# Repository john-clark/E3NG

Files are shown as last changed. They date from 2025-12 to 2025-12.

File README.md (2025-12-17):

# E3NG Repo

This was mirrored from the RH3D website repo because I wanted to have one place to keep track of everything. I have pulled out a lot of the website stuff in order to have just the information I am interested in. This repo uses LFS so if you use the github download zip it will not include the large files.

### This is not meant as an official repo or as anything but my personal E3NG repo

All credits go to the [RH3D E3NG](https://rh3d.xyz/).

If you stumbled upon this that is where you should go for more information.

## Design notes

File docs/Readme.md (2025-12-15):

# Documentation

### Original

While the pdf's that the project puts out are very well put together they lack key information and are not well suited to the build process or the revision process. The author makes changes without producing a change log, sometimes changing key information. It s sort of funny that these files will not open with Adobe, I had to open them with Firefox and then print them to a PDF to open them with Adobe so I could compare the changes. This is not a fun way to do this but I think the project needs to do a better job with the versioning and documentation, some of the information removed is key to the project and there is quite a bit of missing or incorrect information.

### Extracted

!WIP I extracted the LONG pdf files and put them into o and s folders. o is for the old doc and s is the current. I didn't have time to finish going through them, but the o folder has some pages that were removed from the current docs. I hope to eventually finish digging through them and combining them with the web site doc and finally they should be matched up with the models so you can quickly look at the parts that are being explained. !TODO WIP

NOTEs: The printable frame information was removed, and it looks like they settled on the so called ultimate frame. I think this is because the E3NG project has a major flaw with all the corners being printed and therefore subject to no good alignment. The maintainers new project seems to correct this and gets rid of most of the 3d printed parts used in squaring the frame. However with a 3d printed gantry this point is moot since that will also have issues. The revised gantry has several problems compared to the old gantry such as easy of disassembly.

Also if you are going to be printing the bottom skirts you might as well ignore pages 19-20 and 23.

The  Electronics section was so bad I didn't bother to compare.

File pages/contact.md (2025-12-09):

---
title: Contact ✉️
layout: default
nav_order: 110
description: "Reach out to RH3D with questions, feedback, or collaboration ideas. Connect with the maker behind Ender 3 NG, Virtu E3, and other 3D printer upgrade projects."
permalink: /contact
---

<div class="responsive-iframe-container">
  <iframe
          src="https://docs.google.com/forms/d/e/1FAIpQLSdQgB7Aw7cdLq2ng6Stj-KTayaxvqaDmWC6Ourq5sMZkLAirw/viewform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"
          width="100%"
          height="1080px"
          frameborder="0"
          marginheight="0"
          marginwidth="0">
    Loading…
  </iframe>
</div>

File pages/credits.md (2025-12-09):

---
title: Credits
layout: default
nav_order: 60
description: "Discover the makers, contributors, and open-source projects behind E3NG. RH3D thanks the DIY 3D printing community for sharing innovation and inspiration."
permalink: /credits
---
# THANK YOU
{: .text-center }

- Everyone who decides to give support / donates to the project.
- All our Discord members for creating an awesome place to chat and for helping each other.
- Everyone who decides building the printer and contributes to the world of E3NG.
- Bigtreetech
- Creality3D
- [Discovery Sky]

---
Projects used (remixed) in the E3NG.
- [WobbleX] by MirageC
- [Klicky probe] by jlas
- [KlickyPCB dock] by SP1986
- [M4 Extruder] by VoronDesign
- [Sherpa mini] and [Sherpa micro] by Annex Engineering
- [HextrudORT] by MirageC
- [Vz-HextrudORT] by Vez3D
- [ProtoXtruder], [ProtoXtruder 2.0] and [Hummingbird extruder] by nhchiu
- [Klipper]
- [Marlin]

And others.
- [Rolohaun3D] for the inspiration of using linear rods as a structural part of the frame.
- [MirageC], [Vez3D], [eddietheengineer], [VoronDesign], [Prusa3D] and many others for their dedication to research in 3D printing.

[Discovery Sky]: https://github.com/markniu
[WobbleX]: https://github.com/MirageC79/Interfaces-for-WobbleX-integration
[Klicky probe]: https://github.com/jlas1/Klicky-Probe
[KlickyPCB dock]: https://www.teamfdm.com/files/file/729-pcb_klicky_mount/
[M4 Extruder]: https://github.com/VoronDesign/Mobius-Extruder
[Sherpa mini]: https://github.com/Annex-Engineering/Sherpa_Mini-Extruder/
[Sherpa micro]: https://github.com/Annex-Engineering/Sherpa_Micro-Extruder
[HextrudORT]: https://github.com/MirageC79/HextrudORT
[Vz-HextrudORT]: https://github.com/VzBoT3D/Vz-HextrudORT
[ProtoXtruder]: https://www.printables.com/cs/model/436425-protoxtruder
[ProtoXtruder 2.0]: https://www.printables.com/cs/model/822947-protoxtruder-20
[Hummingbird extruder]: https://www.printables.com/cs/model/367706-hummingbird-extruder
[Klipper]: https://www.klipper3d.org/
[Marlin]: https://marlinfw.org/
[Rolohaun3D]: https://github.com/rolohaun/Rook-180

[MirageC]: https://www.youtube.com/@MirageC
[Vez3D]: https://www.youtube.com/@Vez3D
[eddietheengineer]: https://www.youtube.com/@eddietheengineer
[VoronDesign]: https://github.com/VoronDesign
[Prusa3D]: https://github.com/prusa3d

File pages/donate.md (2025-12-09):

---
title: Support the development ❤️
layout: default
nav_order: 99
description: "Support RH3D's open-source development of Ender 3 NG, Virtu E3, and DIY 3D printing projects. Your donation helps keep innovation alive and accessible."
permalink: /donate
---
# SUPPORT THE DEVELOPMENT
{: .text-center }

Ender 3 NG will always be free to use, but developing a project of this size, variability and compatibility is a huge amount of work. It takes lot of time, effort and requires resources to test and improve the design and maintain it up to date.

With your donation, you are helping to keep the project alive, maintained and growing as well as opening the possibility for other future projects. You can use some of the links below.

You can also use affiliate links in the BOM which also helps with no added cost to you.

#### Thank you a lot!
{: .text-center }

<div>
<script type='text/javascript' src='https://storage.ko-fi.com/cdn/widget/Widget_2.js'></script><script type='text/javascript'>kofiwidget2.init('Ko-fi', '#28b5e0', 'E1E1JZ5FS');kofiwidget2.draw();</script> 
</div>
{: .text-center .mt-8 }

<div id="donate-button-container">

<script src="https://www.paypalobjects.com/donate/sdk/donate-sdk.js" charset="UTF-8"></script>
<script>
PayPal.Donation.Button({
env:'production',
hosted_button_id:'LR94TRQXMGW46',
image: {
src:'../assets/images/paypal_donate.png',
alt:'Donate with PayPal button',
title:'PayPal - The safer, easier way to pay online!',
}
}).render('#donate-button');
</script>
</div>
{: .text-center .mt-5 }

Patreon (https://www.patreon.com/RH3D_cz)
{: .text-center }

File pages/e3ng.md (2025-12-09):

---
title: E3NG v1.2
layout: default
has_children: true
nav_order: 20
description: "Transform your Ender 3 into a powerful CoreXY machine with E3NG by RH3D. Reuse up to 78% of original parts for a faster, more precise 3D printing experience."
permalink: /e3ng
---
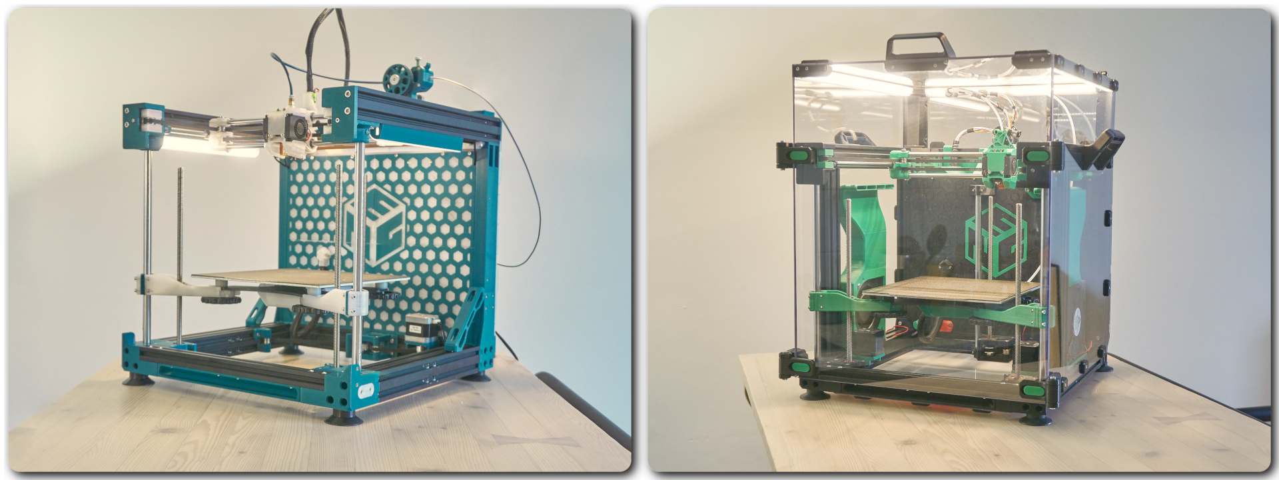
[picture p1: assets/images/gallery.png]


# E3NG (ENDER 3 NG)
{: .text-center }

**Take your old, unused Creality Ender 3 and turn it into something amazing—something fast, powerful, precise, and reliable and enjoy the new level of tinkering.**
{: .text-center .mb-6 }

E3NG is a DIY project focused on reviving up to **78%*** of parts from your original printer and giving them a brand-new purpose. Many of us started with the simple Ender 3, and it taught us a lot—but 3D printing has evolved, and it’s time to step up. That’s exactly what this conversion is all about.

Originally designed for the Ender 3 Pro, it also supports other models like the V2, Neo, and even the non-Pro variant. The goal? Reuse as much as possible and build a machine that’s significantly faster, more reliable, easy to enclose, and still totally upgradable—because let’s face it, not everyone with an Ender 3 is done tinkering.

Whether you go with a low-budget build or max out performance, you’ll turn your Ender 3 into a CoreXY machine that honors its roots—while bringing it into the **Next Generation** of printers.

There are two versions to choose from:
 - **v1.2S (standard)** offers a more streamlined, kit-style approach with clear instructions and a straightforward build path—perfect if you prefer to keep things more simple.
 - **v1.2 (advanced)** is for those who like to go deep into the project, tweak every detail, giving you the flexibility to configure your printer to match your own preferences and setup.

[E3NG v1.2S (standard)]{: .btn .fs-6 .fw-300 .text-yellow-300 .v-align-middle .mr-3 .mb-8 .mt-6 } [E3NG v1.2 (advanced)]{: .btn .fs-6 .fw-300 .text-yellow-300 .v-align-middle .ml-3 .mb-8 .mt-6 }
{: .text-center }

# "NG = NEXT GENERATION"
{: .text-center }

#### PRINTER FEATURES
- Build volume _(X-Y-Z)_: 235 x 235 x 245 mm (max Z depends on the hotend used)
- Printer size _(X-Y-Z)_: 407 x 438 x 440 mm ( 455 x 485 x 548 mm enclosed )
- CoreXY motion system
- Linear rods for X, Y and Z axis.
- Stable Z axis with 3 leadscrews and 3 linear rods.
- Enclosed electronics on the back of the printer.
- DIN rails in electronics compartment for easy organization.
- Anti Z wobble system within the bed carriage.
- Easy to enclose.

#### BONUS FEATURES
- Reuses up to **78%*** of the original parts.
- Fanducts optimised with CFD analysis tools.
- Toolhead compatibility with majority of hotends, extruders and bed probes.
- Toolhead with 4 variants of part cooling - dual 4010, dual 4020, dual 5015, CPAP.
- Files designed for easy printability and functionality.

#### OPTIONAL FEATURES (in the v1.2 - advanced)
- Under bed fan for air circulation and faster chamber heating.
- Active cooling for AB stepper motors.
- Auxiliary fans with 12032 blowers.
- Lasercut metal bed carriage for the best stability.
- Single or triple Z stepper motors.
- and more - see the [CONFIGURATION] options

continue to:
{: .text-right .lh-0 .pt-8 }

[INTO THE PROJECT]{: .btn .fw-300 .fs-6 .text-yellow-300 }
{: .text-right }

---
***up to 78%** = Measured by weight of the parts from stock Ender 3 Pro. The percentage is calculated when reusing the majority of parts incl. motherboard, screen, screws, hotend (which is all possible). When using the required minimum of parts, **68%** is reused.*

*For extra **9%** of part reusage, there are side projects specifically designed to reuse more of the leftover parts - heat set insert press, camera slider (will be released to public later). The number of projects might grow in the future.*

[E3NG v1.2S (standard)]: https://rh3d.xyz/E3NG_v1_2/standard
[E3NG v1.2 (advanced)]: https://rh3d.xyz/E3NG_v1_2/advanced
[INTO THE PROJECT]: https://rh3d.xyz/into.html
[CONFIGURATION]: https://rh3d.xyz/E3NG_v1_2/advanced/config

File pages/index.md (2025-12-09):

---
title: RH3D
layout: home
nav_order: 10
description: "Explore RH3D's custom Ender 3 upgrades and DIY 3D printing projects. Give your printer a second life and join a passionate maker community."
permalink: /
---
# E3NG (ENDER 3 NG)

The legacy design that transforms your basic Ender 3 into a Next Generation machine. Want to keep it simple and affordable or go fully loaded? The choice is yours.

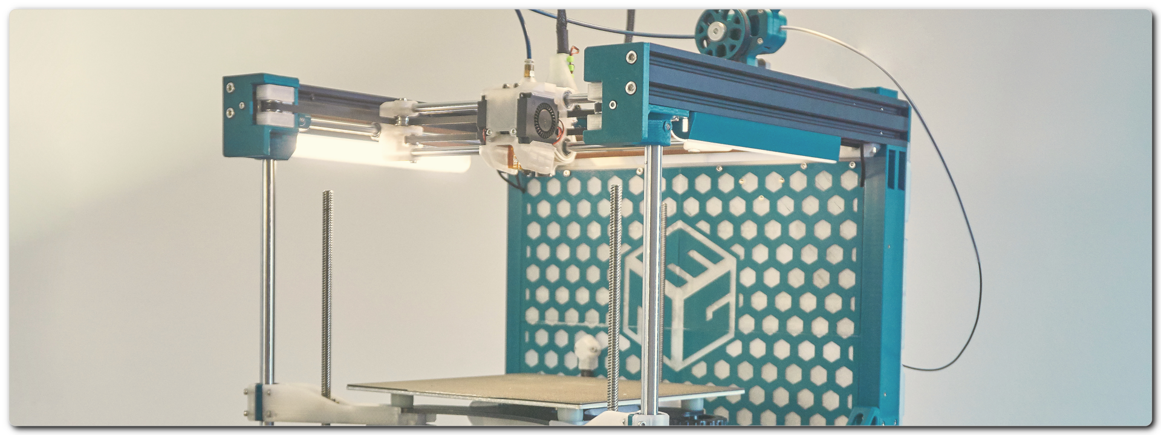
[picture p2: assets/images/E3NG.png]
E3NG (https://rh3d.xyz/e3ng)

{: .text-center }

# VIRTU E3
{: .mt-9 }

The second-generation hero, built to revive all the unused Enders. Purity, speed, precision — this is Virtu.

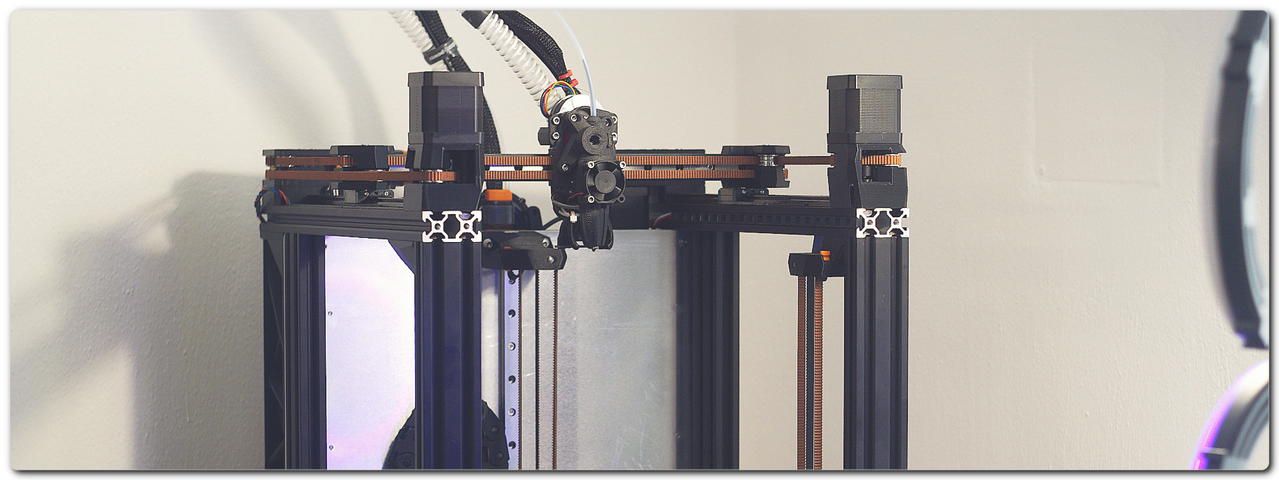
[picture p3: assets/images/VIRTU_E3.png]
VirtuE3 (https://rh3d.xyz/virtu)

{: .text-center }

---
# WELCOME!
{: .text-center }

If you're into 3D printing, love to tinker, and enjoy building things yourself, you’re in the right place.

What began as a hobby and a personal project quickly evolved into a true passion. This site is where you'll find all my major designs, complete with the information you need. Feel free to explore the site, check out the YouTube and Instagram, and join our amazing community on Discord!

[YouTube]{: .btn .fw-400 .text-yellow-300 .v-align-middle .mb-8 } [Instagram]{: .btn .fw-400 .text-yellow-300 .v-align-middle .ml-5 .mr-5 .mb-8 } [Join the Discord]{: .btn .fw-400 .text-yellow-300 .v-align-middle .mb-8 }
{: .text-center }

---
## About RH3D

Hi! I’m Radek—engineer, architect, woodworker, and maker by nature. I was born into a family of engineers in the Czech Republic, and from a young age, I found joy in creating. Whether it was building something with my hands or dreaming up designs on paper, I was always drawn to the process of turning ideas into reality.

My journey has taken me through engineering, woodworking, and ultimately back to my original profession—architecture. But beyond the workshops and design boards, I’m also a proud husband and loving father. My family keeps me grounded and inspired, and they’ve been my biggest supporters through every prototype and late-night tinker session.

## How did I get into 3D printing?

I was always fascinated by the technology, but without a clear use case, I couldn't justify owning a printer. That changed when I got an old Ender 3 Pro to support a few side projects in my woodworking business. Who could’ve guessed I’d get completely hooked—printing, upgrading, modifying... like most of the Ender 3 owners, right?

## The first Ender 3 NG

Once you dive in, it’s tough to stop. I realized there were more capable designs within reach. After plenty of research, modifications, and testing, the Ender 3 NG was born. It started as a personal project to convert an Ender 3 into an enclosed CoreXY machine on a budget—but it grew into something far more meaningful. This journey has led me to create amazing things, build a thriving community, and connect with passionate people from around the world.

[Join the Discord]: https://discord.com/invite/Zkvu6uu2AR
[Instagram]: https://www.instagram.com/RH3D_cz
[YouTube]: https://www.youtube.com/@RH3D_cz?sub_confirmation=1

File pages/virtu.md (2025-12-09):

---
title: VIRTU E3
layout: default
has_children: false
nav_order: 40
description: "Turn your Ender 3 into an unstopable coreXY machine! Speed, precision, purity - that is Virtu E3 by RH3D."
permalink: /virtu
---
# VIRTU E3
{: .text-center }

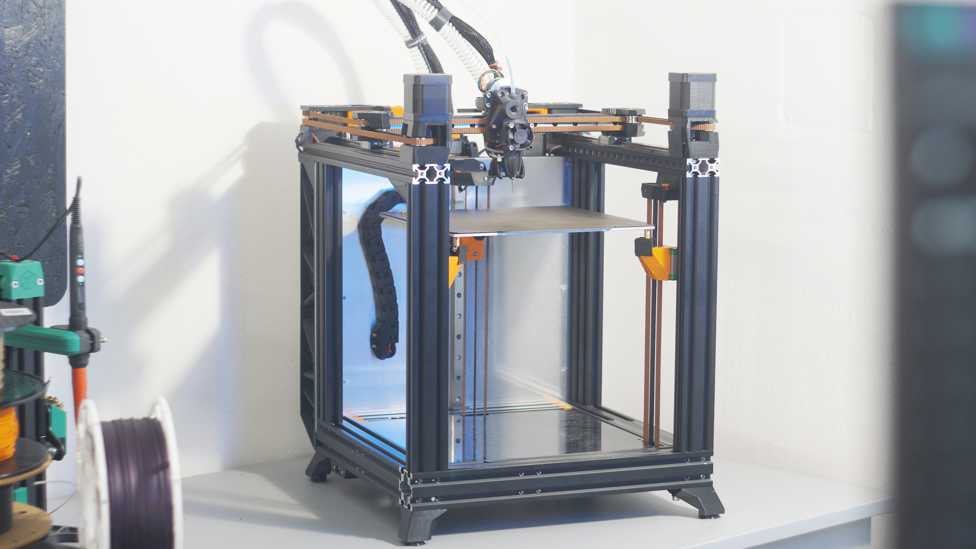
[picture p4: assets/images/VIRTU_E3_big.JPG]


#### CURRENTLY IN DEVELOPMENT AND TESTING
{: .text-center }

---

*Thank you to everyone who helps bringing such projects into reality, especially all my Patreon members and supporters, but also companies like Fabreeko, BigTreeTech, LDO motors, FilamentPM.*

*Thank you all, who are interested into my projects!*

If you also want to help supporting the development, you can do so through any of the [DONATE](https://rh3d.xyz/donate) options. Any kind of support is greately appreciated.
{: .text-center }

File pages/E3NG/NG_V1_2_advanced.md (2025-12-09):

---
title: v1.2 - (advanced)
layout: default
parent: E3NG v1.2
has_children: true
nav_order: 30
description: "Customize your E3NG v1.2 CoreXY printer with modular upgrades, advanced configurations, and full control over sourcing. A flexible DIY platform for expert builders."
permalink: /E3NG_v1_2/advanced
---

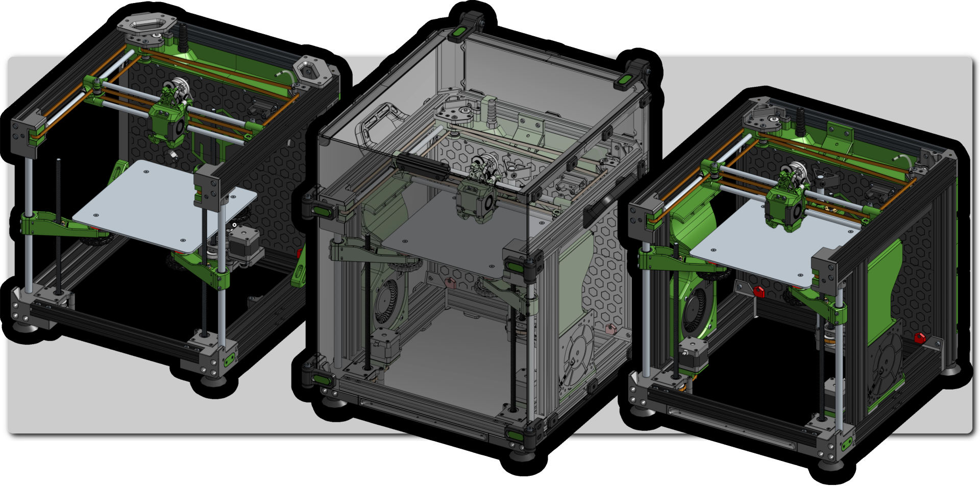
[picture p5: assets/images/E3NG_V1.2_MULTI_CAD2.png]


# E3NG v1.2
{: .text-center }
#### v1.2 = advanced version (customisable)
{: .text-center }

The v1.2 "advanced" is built for more experienced users who value modularity, higher configuration control, and overall flexibility. Unlike the standard version, v1.2 is not bound by kit constraints and instead offers a configurator-driven workflow that helps you setup the printer build based on your own preferences and gives you more customisation options.

Builders may choose to start with a different frame setup or incorporate upgrades such as LEDs, auxiliary cooling, stepper motor cooling, CNC-cut bed carriage, triple-Z motor configuration and others. These options are documented and categorized in the official configuration guide, allowing the end-user to balance cost, complexity, and performance according to their specific goals.

Due to the diversity of possible configurations, sourcing for the v1.2 requires manual part selection. To assist in this process, the configurator generates a tailored Bill of Materials with direct links to vetted sellers and clearly annotated specifications. This ensures that while the build is more demanding, it remains accessible to users with a clear roadmap.

The v1.2 advanced variant is best described as a platform for tinkering, experimentation, personalization, and performance tuning—offering high degree of flexibility in the E3NG family.

continue to:
{: .text-right .lh-0 .pt-8 }

[CONFIGURATION]{: .btn .fs-6 .fw-300 .text-yellow-300 }
{: .text-right }

[CONFIGURATION]: https://rh3d.xyz/

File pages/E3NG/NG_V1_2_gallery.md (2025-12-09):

---
title: Gallery
layout: default
parent: E3NG v1.2
#has_children: true
nav_order: 1
description: "Browse E3NG v1.2 build photos and wallpapers. See real CoreXY conversions of Ender 3 printers powered by RH3D’s open-source designs and community creativity."
permalink: /E3NG_v1_2/gallery
---
# WALLPAPERS
{: .text-center }

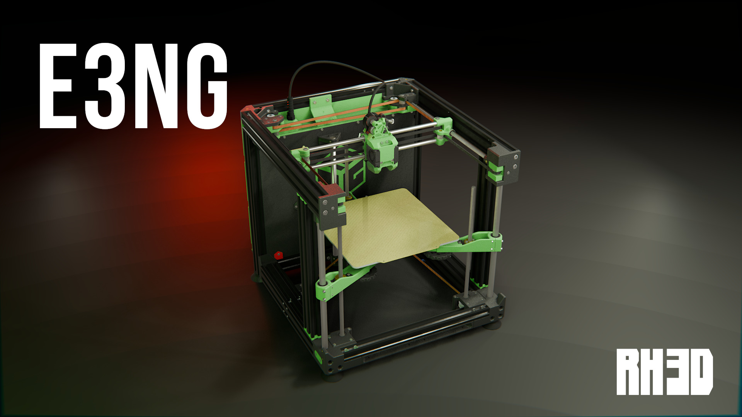
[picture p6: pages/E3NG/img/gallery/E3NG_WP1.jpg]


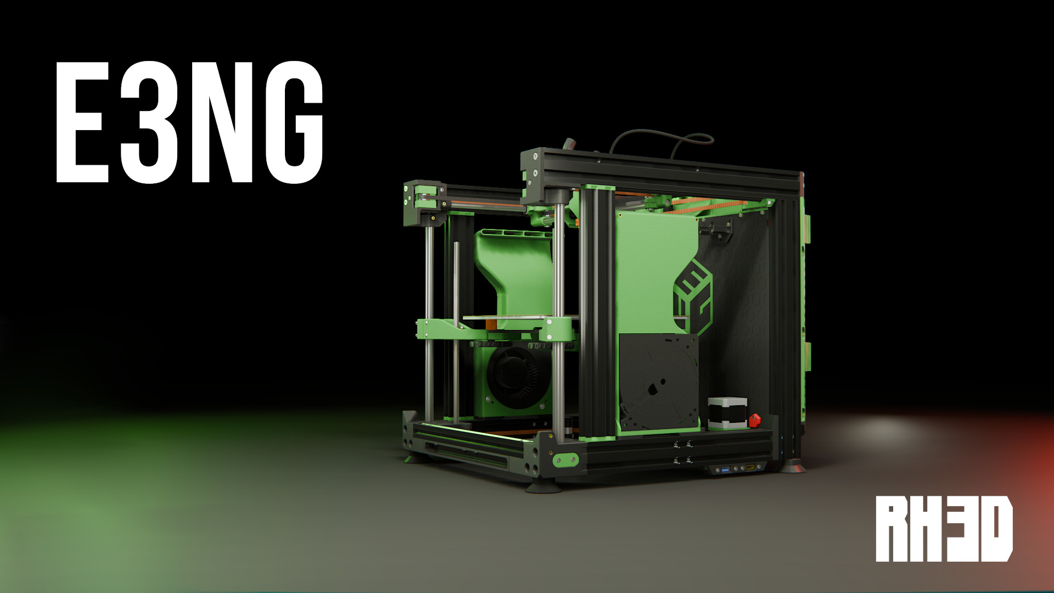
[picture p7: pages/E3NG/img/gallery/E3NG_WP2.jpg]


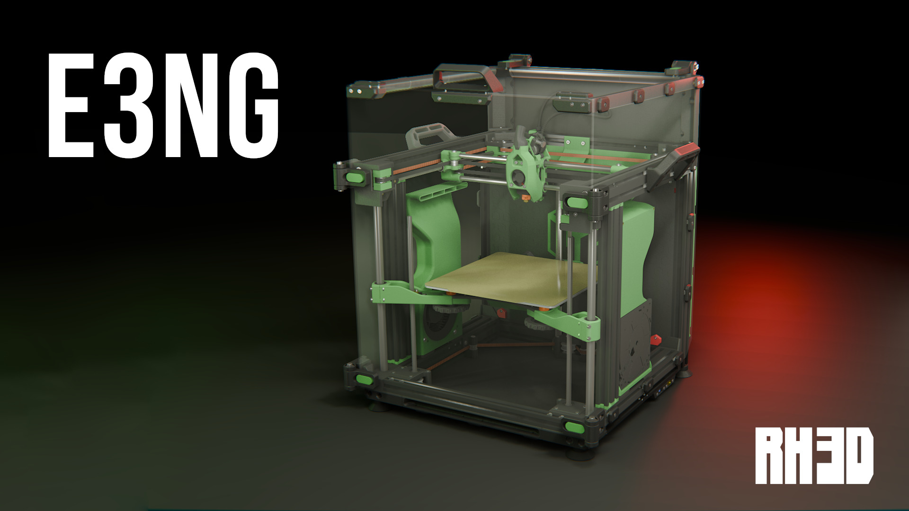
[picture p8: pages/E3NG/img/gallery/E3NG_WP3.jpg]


# PHOTOS
{: .text-center }

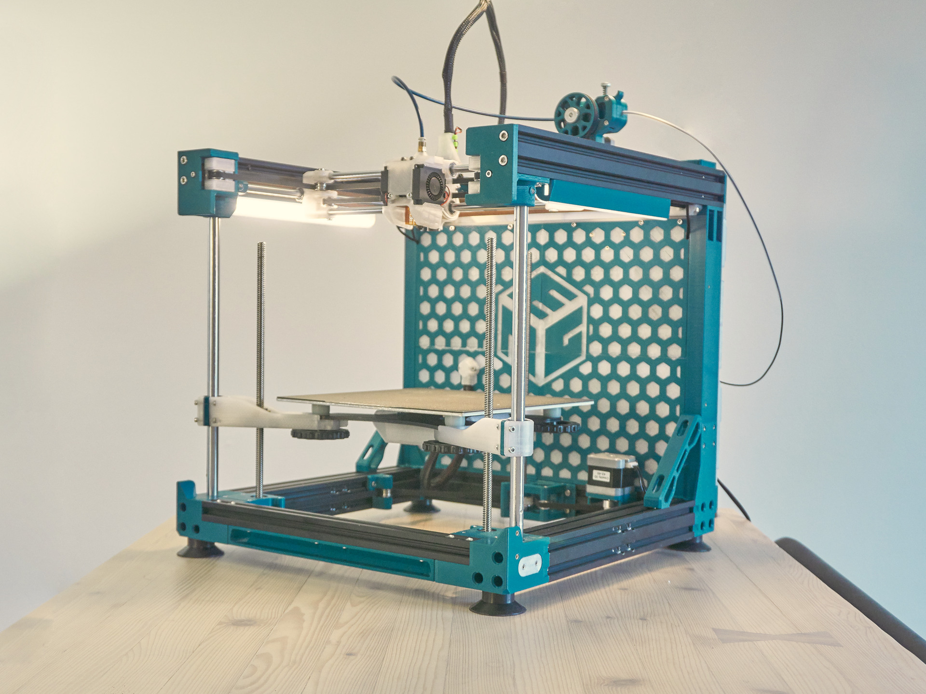
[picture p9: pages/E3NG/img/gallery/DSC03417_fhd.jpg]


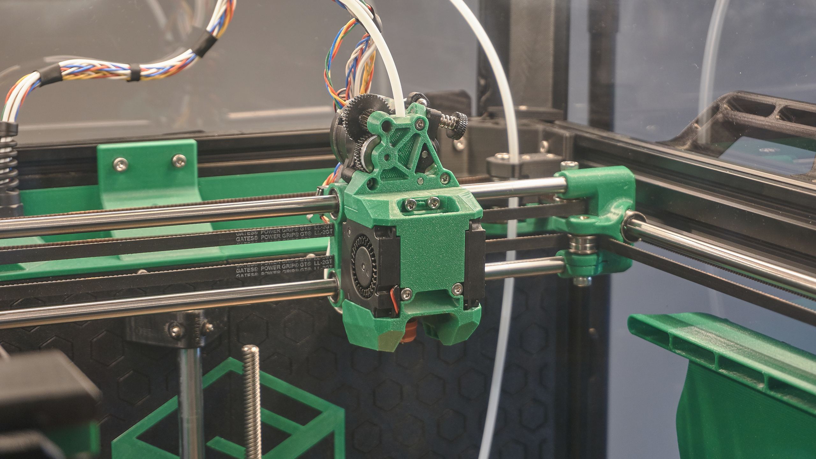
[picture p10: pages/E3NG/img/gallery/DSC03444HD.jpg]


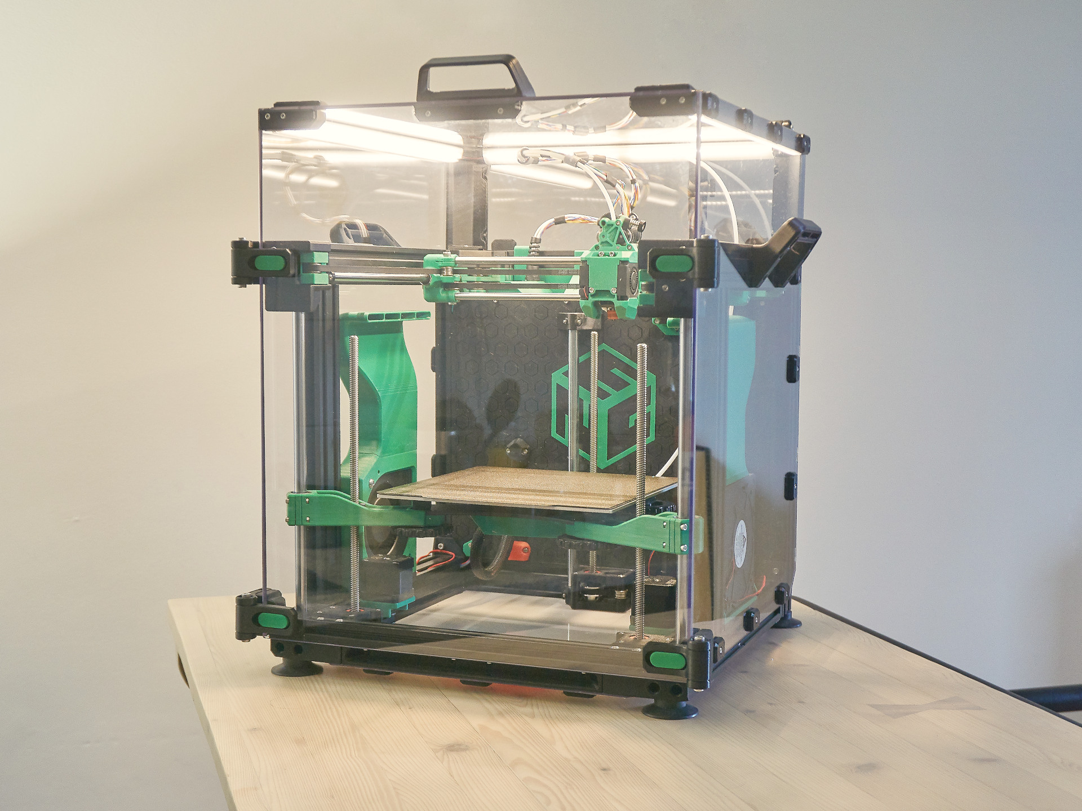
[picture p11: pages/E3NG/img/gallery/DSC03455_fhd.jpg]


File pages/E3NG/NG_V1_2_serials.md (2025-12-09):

---
title: Serial numbers
layout: default
parent: Final steps
#has_children: true
nav_order: 30
description: "Apply for an official serial number for your E3NG v1.2 build. Showcase a finished CoreXY printer and join the lineup of verified RH3D makers."
permalink: /E3NG_v1_2/final_setup/serial_number
---
# SERIAL NUMBERS
{: .text-center }

Just like many of the other known DIY printers, you can get serial number even for your own Ender 3 NG.
The main list of serial numbers and announcements are hosted on Discord server but it is not required to join the Discord server.

All you have to do is meet the requirements and apply for the serial in the link below.

#### Requirements to obtain a serial number.
- Majority of the printer must be based on the Ender 3 NG project. Some smaller mods are allowed but the main goal of serial numbers is to participate in the official project path so highly modified printer may not be approved. The main frame and the X, Y and Z motion systems have to be stock or with minor changes, although you can use different toolhead.
- The printer must be fully functional and tuned to print well without major noticable issues or print quality issues.
- The printer must be finished and not look half done even though it is printing fine. No hanging wires and uncovered electronics are allowed.
- You must upload a video of the printer running where it is well visible and also show that it is actualy printing. Print something at least few centimeters in size.

{: .note }
Remember, it is not a race to get your serial number as soon as possible but rather an oportunity to present your new and pretty printer and add to the line of other nicely build printers.

# SERIAL NUMBER REQUEST
{: .text-center }

To request the serial number, fill the form on the link below:
{: .text-center .lh-0 }

[REQUEST A SERIAL]{: .btn .fs-6 .fw-300 .text-yellow-300 }
{: .text-center }

After your serial number request is succesfully processed, it will be announced on discord channel with provided information and you will be notified, if you are not a member of our Discord server, don't forget to include your e-mail address.

[REQUEST A SERIAL]: https://forms.gle/4JTC2YdJKMqADTAX6

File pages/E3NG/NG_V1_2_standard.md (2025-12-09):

---
title: v1.2S - (standard)
layout: default
parent: E3NG v1.2
has_children: true
nav_order: 20
description: "E3NG v1.2S offers a guided CoreXY upgrade for your Ender 3. Build faster with curated kits, simplified instructions, and streamlined compatibility."
permalink: /E3NG_v1_2/standard
---
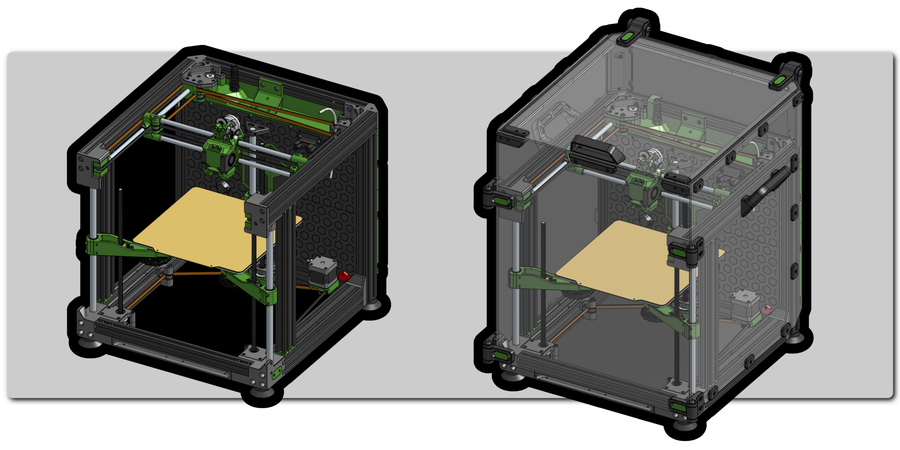
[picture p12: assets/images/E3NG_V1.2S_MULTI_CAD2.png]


# E3NG v1.2S
{: .text-center }
#### v1.2S = standard version (kit-based)
{: .text-center }

The v1.2S variant of the E3NG platform is intended for users who prioritize clarity and a streamlined assembly process. This configuration offers a guided path toward transforming an Ender 3 (Pro, V2, Neo, or non-Pro) into a CoreXY machine without the complexity of open-ended customization. It has been specifically designed to reduce the sourcing burden through predefined kits, simplified documentation, and a well-tested selection of parts—allowing users to focus on assembly and performance tuning rather than studying all the advanced options and their compatibility.

This version includes structured instructions, a standardized Bill of Materials, and multiple kit options covering either full builds or partial upgrades. You can download the version specific package of printable parts and even firmware files. The mechanical and motion platform remains the same as in the advanced variant, so it is easy to perform upgrades later, once you get familiar with the printer.

While customization is possible post-build, the v1.2S prioritizes user experience and accessibility, making it an excellent entry point into the E3NG ecosystem for those new to CoreXY systems or those seeking a dependable upgrade path from the classic Ender 3 design.

## WHAT IS THE CONFIGURATION FOR E3NG V1.2S?
*Comparing the setup with v1.2 (advanced), these are the v1.2S settings for the [configurator](https://rh3d.xyz/E3NG_v1_2/advanced/config).*

<details>
  <summary>
    <h3 style="display:inline-block; margin-left:1.5em;">
      E3NG v1.2S configuration
    </h3>
  </summary>

  <h3>BASE BUILD</h3>
<p style="margin:1.5em 0 0 1.5em; line-height:1; display:table;"><span style="display:table-cell; width:180px; font-weight:bold;">
      BASE PRINTER:</span><span style="display:table-cell;">
      Ender 3 Pro / Ender 3 V2 / Ender 3 (all compatible)</span></p>
<p style="margin:0.5em 0 0 1.5em; line-height:1; display:table;"><span style="display:table-cell; width:180px; font-weight:bold;">
      ENCLOSURE:</span><span style="display:table-cell;">
      Depends on the kit (some have it included, some separate)</span></p>
<p style="margin:0.5em 0 0 1.5em; line-height:1; display:table;"><span style="display:table-cell; width:180px; font-weight:bold;">
      FRAME:</span><span style="display:table-cell;">
      Ultimate frame</span></p>
<p style="margin:0.5em 0 0 1.5em; line-height:1; display:table;"><span style="display:table-cell; width:180px; font-weight:bold;">
    Z AXIS RODS:</span><span style="display:table-cell;">
    3x12mm rod</span></p>
<p style="margin:0.5em 0 0 1.5em; line-height:1; display:table;"><span style="display:table-cell; width:180px; font-weight:bold;">
    BED CARRIAGE:</span><span style="display:table-cell;">
    Stock E3 bed carriage</span></p>
<p style="margin:0.5em 0 0 1.5em; line-height:1; display:table;"><span style="display:table-cell; width:180px; font-weight:bold;">
    Z WOBBLE COMP.:</span><span style="display:table-cell;">
    Flexi joint</span></p>
<p style="margin:0.5em 0 0 1.5em; line-height:1; display:table;"><span style="display:table-cell; width:180px; font-weight:bold;">
    Z AXIS DRIVE:</span><span style="display:table-cell;">
    1 stepper - 1140 mm belt</span></p>
<p style="margin:0.5em 0 0 1.5em; line-height:1; display:table;"><span style="display:table-cell; width:180px; font-weight:bold;">
    LEADSCREW PULLEYS:</span><span style="display:table-cell;">
    Aluminium</span></p>
<p style="margin:0.5em 0 0 1.5em; line-height:1; display:table;"><span style="display:table-cell; width:180px; font-weight:bold;">
    BOARD MOUNT:</span><span style="display:table-cell;">
    BTT SKR mini E3 v2 (but has extra hardware for other options)</span></p>

  <h3>TOOLHEAD</h3>
<p style="margin:1.5em 0 0 1.5em; line-height:1; display:table;"><span style="display:table-cell; width:180px; font-weight:bold;">
      COOLING:</span><span style="display:table-cell;">
      2x 4010</span></p>
<p style="margin-left:1.5em; line-height:0.5;">Other toolhead parts (hotend, probe, extruder) are not included - the choice is yours.</p>

  <h3>MODS / UPGRADES</h3>
<p style="margin:1.5em 0 0 1.5em; line-height:1; display:table;"><span style="display:table-cell; width:180px; font-weight:bold;">
      STEPPER COOLING:</span><span style="display:table-cell;">
      No cooling</span></p>
<p style="margin:0.5em 0 0 1.5em; line-height:1; display:table;"><span style="display:table-cell; width:180px; font-weight:bold;">
      FRAME BRACES:</span><span style="display:table-cell;">
      No</span></p>
<p style="margin:0.5em 0 0 1.5em; line-height:1; display:table;"><span style="display:table-cell; width:180px; font-weight:bold;">
      HANDLES:</span><span style="display:table-cell;">
      No</span></p>
<p style="margin:0.5em 0 0 1.5em; line-height:1; display:table;"><span style="display:table-cell; width:180px; font-weight:bold;">
      LED LIGHTS:</span><span style="display:table-cell;">
      No LED</span></p>
<p style="margin:0.5em 0 0 1.5em; line-height:1; display:table;"><span style="display:table-cell; width:180px; font-weight:bold;">
      AUX COOLING:</span><span style="display:table-cell;">
      No</span></p>
<p style="margin:0.5em 0 0 1.5em; line-height:1; display:table;"><span style="display:table-cell; width:180px; font-weight:bold;">
      BED WIRING - WAGO:</span><span style="display:table-cell;">
      No - stock cables</span></p>
<p style="margin:0.5em 0 0 1.5em; line-height:1; display:table;"><span style="display:table-cell; width:180px; font-weight:bold;">
      UNDER BED FAN:</span><span style="display:table-cell;">
      No</span></p>
<p style="margin:0.5em 0 0 1.5em; line-height:1; display:table;"><span style="display:table-cell; width:180px; font-weight:bold;">
      AUTO Z - VORON:</span><span style="display:table-cell;">
      No</span></p>
</details>

continue to:
{: .text-right .lh-0 .pt-8 }

[SOURCING PARTS]{: .btn .fs-6 .fw-300 .text-yellow-300 }
{: .text-right }

[SOURCING PARTS]: https://rh3d.xyz/E3NG_v1_2/standard/sourcing_parts

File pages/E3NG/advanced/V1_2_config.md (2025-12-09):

---
title: Configuration
layout: default
parent: v1.2 - (advanced)
grand_parent: E3NG v1.2
has_children: false
nav_order: 10
description: "Configure your advanced E3NG v1.2 CoreXY build with modular options for frame, toolhead, cooling, and accessories. Use the RH3D configurator to tailor your upgrade."
permalink: /E3NG_v1_2/advanced/config
---
# PRINTER CONFIGURATION
{: .text-center }
[CONFIGURATOR DOWNLOAD]{: .btn .fs-6 .fw-300 .mt-8 .text-yellow-300 }
{: .text-center }
_last updated: 2025.02.17_{: .fs-3 .mt-0 .fw-300 }
{: .text-center }

<details>
    <summary><h4 style="display:inline-block;margin-left:1.5em"> CHANGELOG </h4></summary>
    <p>2025.02.17 - Fixed screws for the 2040 frame with Ender 3 vs Pro vs V2 (M5x30 BHCS)</p>
    <p>2024.10.25 - Added Funssor kits / Updated all current prices in BOM / fixed BTT Eddy printed mounts</p>
    <p>2024.08.19 - Added Fushi bearing and shaft kit / changed RDBB linear rods for Fushi linear rods incl 12x320 mm / fixed link for LED strips</p>
    <p>2024.08.15 - Initial public release</p>
</details>

*You will be guided through all the steps in the configurator and you will get helpful and detailed information for all the available options. This page aims to explain differences between options in more detail, but their effect on the BOM or required parts will show up in the configurator file.*

<details>
    <summary><h4 style="display:inline-block;margin-left:1.5em"> WHAT IS THE CONFIGURATOR, HOW DOES IT WORK? </h4></summary>
<p>CONFIGURATOR is an all in one interactive spreadsheet that includes Configurator, Bill of material, Printed parts and list of verified/approved kits.
The Configurator will, based on your setup, automatically calculate the right quantities in the Bill of Material, show you the right parts to print and even the estimated cost of the BOM and the amount of filament needed. There are two macros included to show/hide unused parts to better organise the table but they are not neccessary to run if you have concerns.</p>
<p>BOM also includes links to buy parts - links are affiliate and help by a small amount to the project with no added cost to you.</p>
<p>The default values are the recommended ones for a good price-performance ratio. Of course, otherwise I would recommend to build the best performing version.</p>
</details>

The configuration is divided into three sections:

[BASE BUILD]{: .btn .fs-5 .fw-300 .text-yellow-300 .mr-7 .px-6 }
[TOOLHEAD]{: .btn .fs-5 .fw-300 .text-yellow-300 .mr-7 .px-6 }
[MODS / UPGRADES]{: .btn .fs-5 .fw-300 .text-yellow-300 .px-6 }
{: .text-center }

{: .note }
All the pictures bellow are higher resolution, so you can zoom in or right click - Open image in new tab/window - to view it in more detail.

---
# BASE BUILD
{: .text-center }

#### BASE PRINTER
Supported and tested printers for the conversion. Compatibility with other printers will be verified and tested over time so if you decide to use a different one for the conversion and want to help with the implementation, please give me feedback. There are also dimensions for the aluminium extrusions in the BOM, so you can check the compatibility yourself or even build the printer from scratch.
- Creality Ender 3 - has 2040 x 330 mm extrusion for Y axis - printed spacer is used.
- Creality Ender 3 Pro - default, has 4040 x 350 mm extrusion for Y axis.
- Creality Ender 3 V2 - some have shorter 4040 extrusion for Y axis - printed spacer is used.

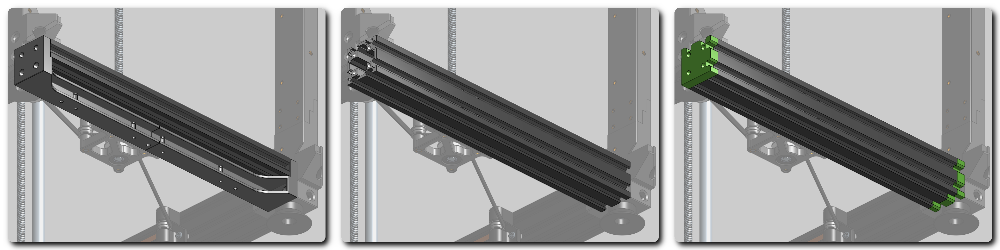
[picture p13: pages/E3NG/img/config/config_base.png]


#### ENCLOSURE
Choosing to enclose the printer or not. V2 style enclosure is better designed and simpler while also adding to the frame rigidity. For the best experience, recommended polycarbonate panels are 4mm thick + 5mm for the front door. Rear electronics cover can be 3mm.

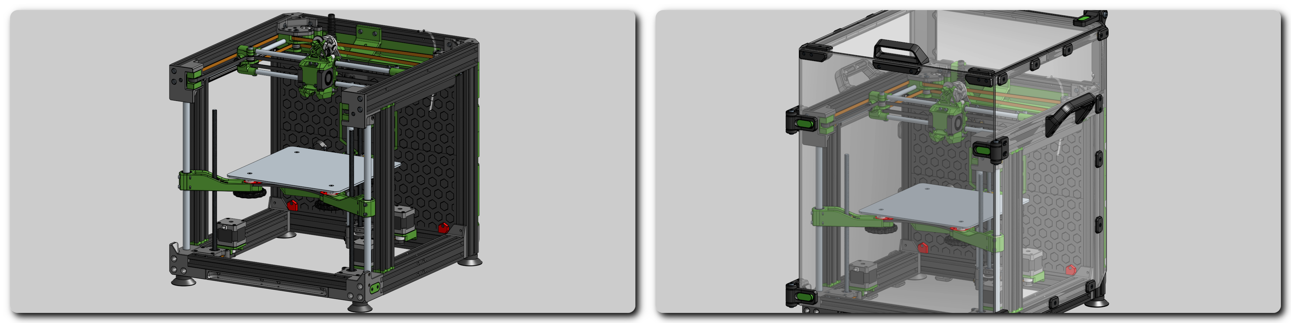
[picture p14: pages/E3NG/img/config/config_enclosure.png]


#### FRAME
- Printed verticals - legacy version where you don't need to buy extra extrusions. Depending on your filament and market prices, it can also be the cheapest option.
- 2040 upgrade - first stage upgrade with additional V-slot extrusion. Adds rigidity to the frame and reduces printing parts. Requires drilling and tapping.
- Ultimate frame - RECOMMENDED - all you need for the best performance, adds two more extrusions to the front. Requires more driling and tapping.

<details>
    <summary><h4 style="display:inline-block;margin-left:1.5em;color:#0096FF;font-weight:bold"> TIP </h4></summary>
<p>For Ultimate frame, you are also buying 300 mm V-slot extrusions which fit into 310 mm space with printed spacers for ease of buying the common size. If you are ordering custom extrusions or cutting them yourself, you can instead use 310 mm extrusions without spacers.</p>
</details>

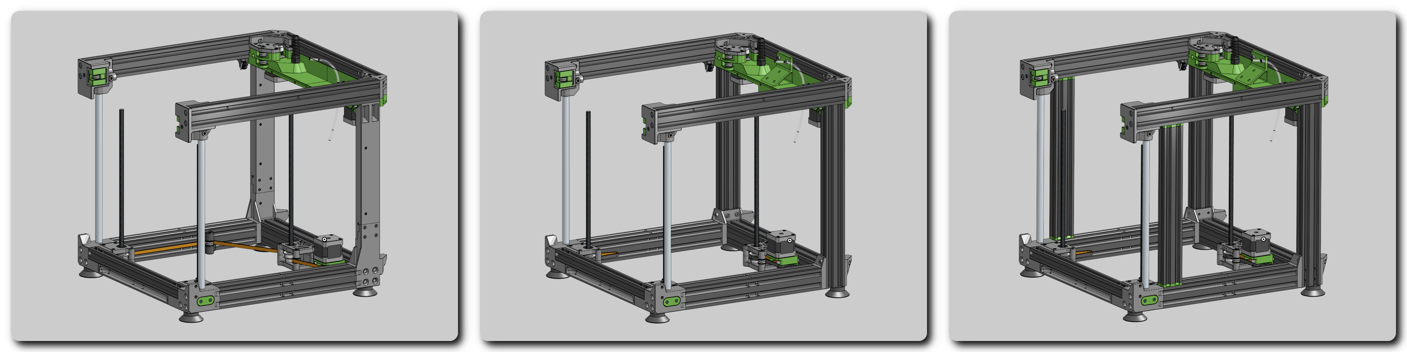
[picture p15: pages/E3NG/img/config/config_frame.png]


#### Z AXIS RODS
- 2x12 mm rod - legacy version - simple setup that works well enough if your leadscrews are not extremely bent, it also saves few dollars.
- 3x12 mm rod - RECOMMENDED - uses linear rod at the rear leadscrew, makes the bed carriage more stable. This is required if you plan to use tilting bed _(once it is released)_.

<details>
    <summary><h4 style="display:inline-block;margin-left:1.5em;color:#0096FF;font-weight:bold"> TIP </h4></summary>
<p>For 3x12 mm rod option, the rear rod is 320 mm long to preserve the toolhead motion over the entire area. While this is not a common size, the BOM lists some options but if you cannot buy 320 mm version and you are unable to cut a 350 mm rod, the design also allows to use 300 mm rod but then it is only sunk in by 7,5 mm on each side. While this will still work, I recommend using a 320 mm option for better reliability.</p>
</details>

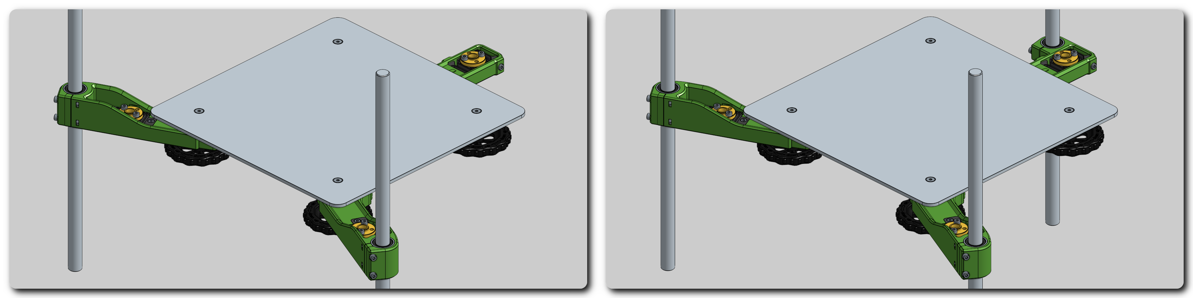
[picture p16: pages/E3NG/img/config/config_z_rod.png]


#### BED CARRIAGE
- Printed - although it works, it is not recommended. It is a backup option for people who cannot use one of the others.
- Stock E3 bed carriage - RECOMMENDED - reuse the stock Ender's bed carriage. Requires drilling and tapping.
- Metal carriage - cut with laser od water, most rigid option, if you want to get the best out of your printer.
- _Z-tilt bed - in development_

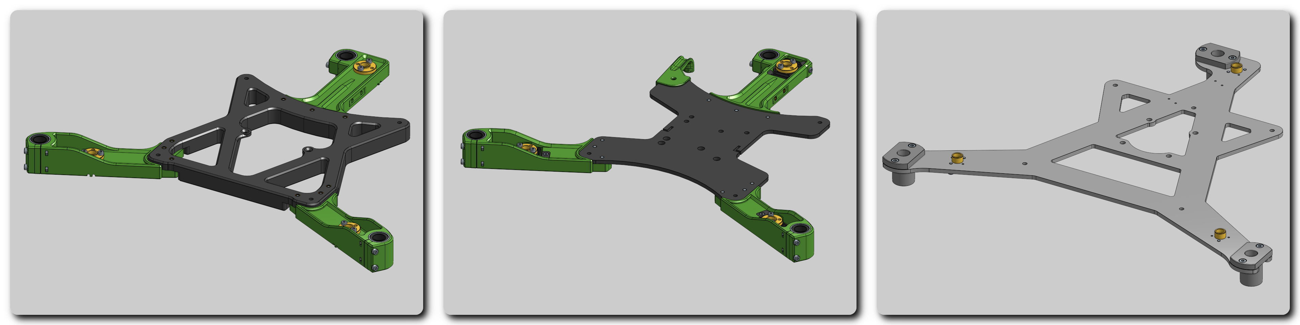
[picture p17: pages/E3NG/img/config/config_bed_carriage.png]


#### Z WOBBLE COMPENSATION
- None - no Z wobble compensation, T8/8 nuts mounted directly.
- Flexi joint - RECOMMENDED - printed flexible inserts that compensate leadscrew runout.
- WobbleX - more efficient solution by MirageC, but it reduces the max Z by around 22 mm.

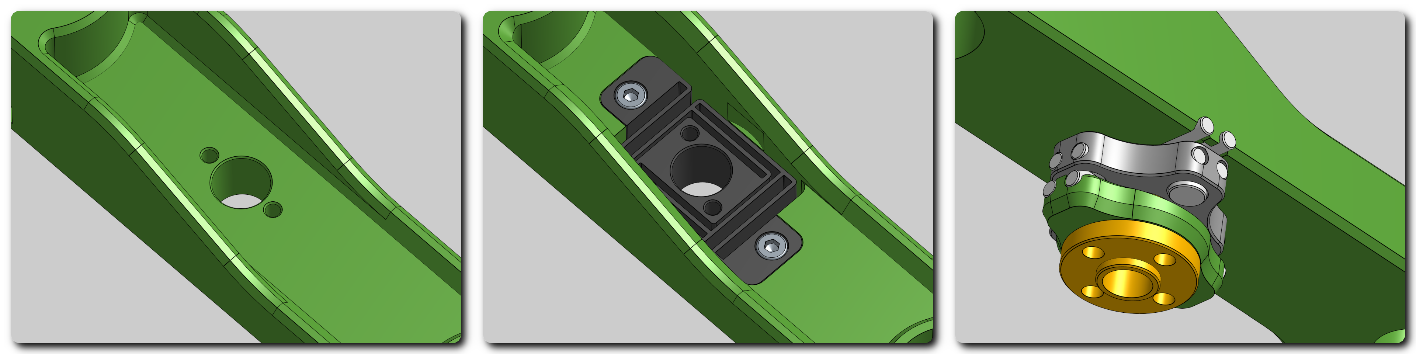
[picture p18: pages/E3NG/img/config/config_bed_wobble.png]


#### Z AXIS DRIVE
- 1 stepper - RECOMMENDED - more foolproof and simple solution with one stepper and long belt driving all 3 leadscrews, also cheaper.
- 3 steppers - for individualy driven leadscrews and Z-tilt option. This is required if you plan to use tilting bed _(once it is released)_, but currently this option isn't recommended as there is no compliant mechanism in the bed carriage.

<details>
    <summary><h4 style="display:inline-block;margin-left:1.5em;color:#FF0000;font-weight:bold"> WARNING! </h4></summary>
<p>When using a 3 stepper option with a bed carriage that isn't properly designed for tilt, there is a significant chance of excessive load on LM12UU bearings and leadscrews which can result in binding, increased friction and faster wear of components or worse print quality if your bed is not aligned properly.</p>
<p>If you select this option, be very careful, make sure your bed is aligned well resulting in a minimal tilt of the bed carriage (not only the bed plate) and check the function/alignment regularly.</p>
<p>Do at your own responsibility, you have been warned.</p>
</details>

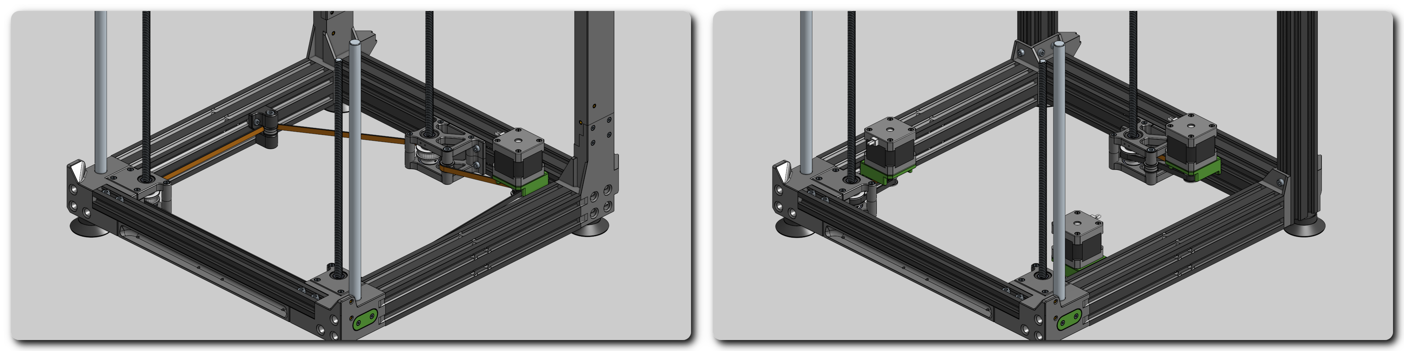
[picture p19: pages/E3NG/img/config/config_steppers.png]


#### LEADSCREW PULLEYS
- Printed - legacy version - cheap and simple option but for good performance it is important to verify that there is no ovality in pulleys and the print is precise.
- Aluminium - RECOMMENDED - precise aluminium pulley equals precise leadscrew rotation.

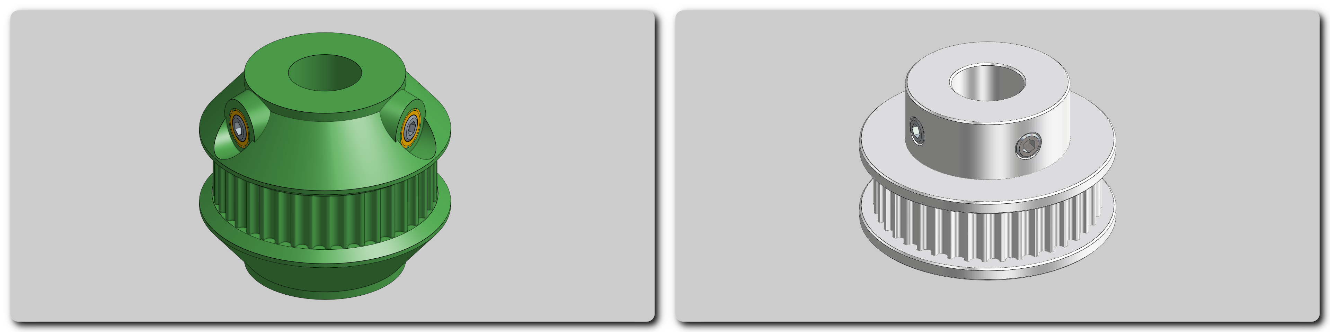
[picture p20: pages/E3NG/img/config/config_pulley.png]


#### PSU THICKNESS
- 30 mm - thinner Meanwell PSU used in Ender 3 Pro and in some Ender 3 V2
- 50 mm - thicker PSU used in Ender 3 and in some Ender 3 V2

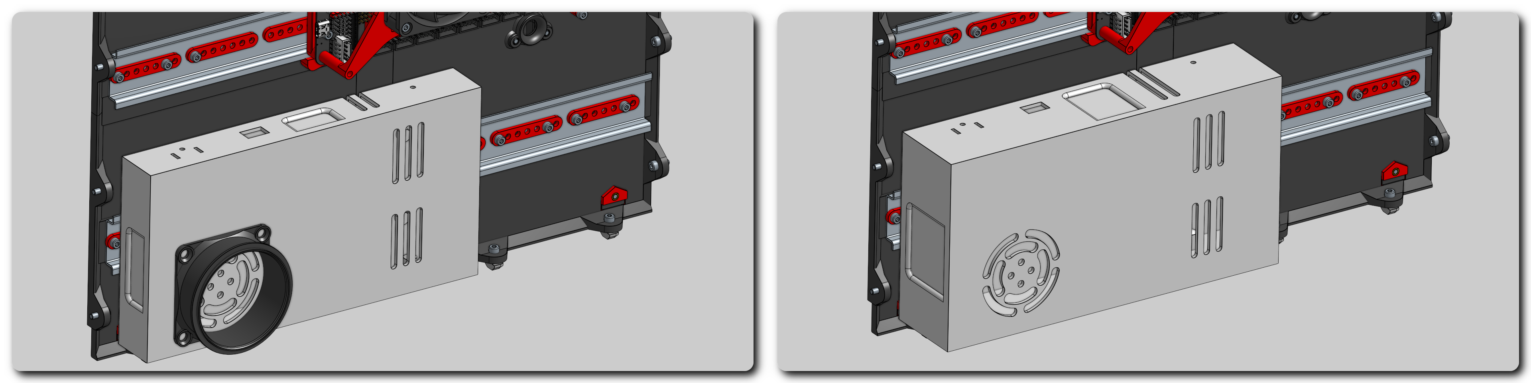
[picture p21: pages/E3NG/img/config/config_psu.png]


#### BOARD MOUNT
Currently there are setups for only few motherboards but more will be directly supported in the future. The supported board has DIN rail mount along with cooling fan holder and there is also a FW setup available. But being the boards mounted on DIN rails, it is easy to use any other board.
- BTT SKR mini E3 v2
- BTT SKR3EZ
- BTT Octopus
- Other - includes universal cooling fan housing mounted directly on the rear panel.

<details>
    <summary><h4 style="display:inline-block;margin-left:1.5em;color:#0096FF;font-weight:bold"> TIP </h4></summary>
<p>Apart from the main board mount you may also need mounts for other electronics. Have a look at EXTRAS folder, there are Raspberry Pi, SSR, 5V PSU and other mounts.</p>
</details>

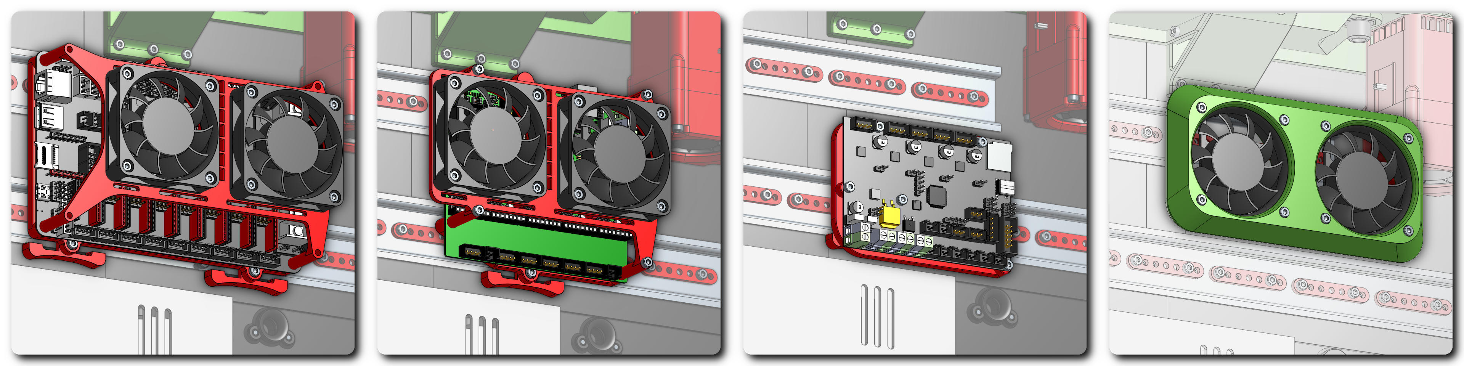
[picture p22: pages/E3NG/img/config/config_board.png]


---
# TOOLHEAD
{: .text-center }
Toolhead is put together with separate parts for mounting each of the components which makes it super easy to alternate between different types of hardware or doing a maintenance.

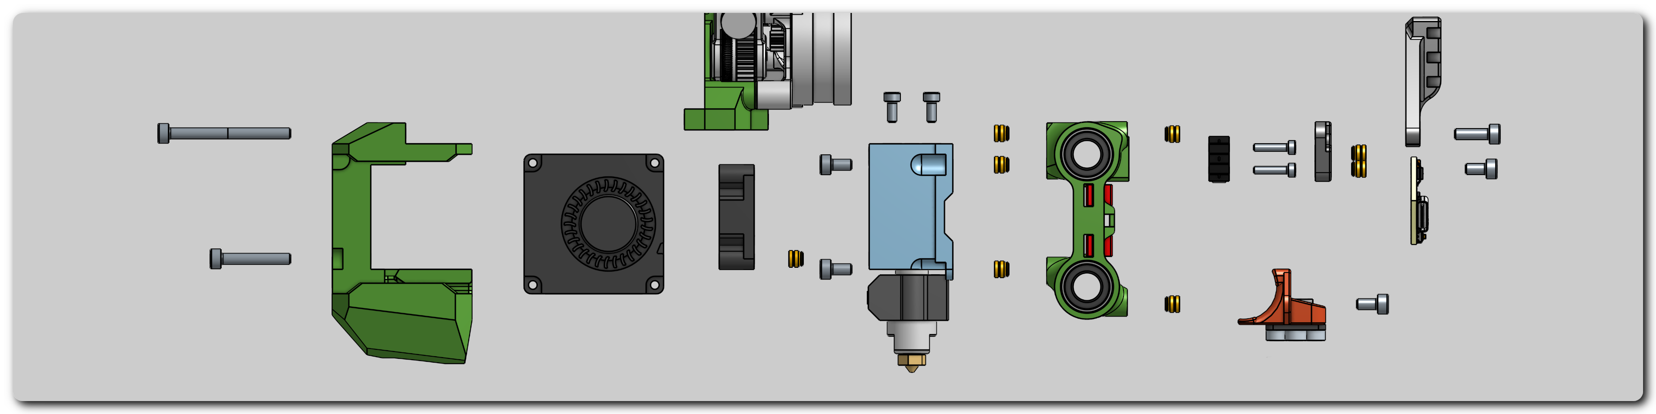
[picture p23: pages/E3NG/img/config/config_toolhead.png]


#### HOTEND
Select the hotend you want to use, it is generaly recommended to use hotend with higher flow.

<details>
    <summary><h4 style="display:inline-block;margin-left:1.5em;color:#5ca33c;font-weight:bold"> COMPATIBLE HOTENDS </h4></summary>
<p>Listed hotends were directly tested in the CAD design or/and in real life and have a specific mount, so it is verified they can be used. Some of the mount styles are widely used so the real compatibility list will be even bigger.</p>
<ul style="margin-left:2em;font-size:14px">
<li>BambuLab hotends</li>
<li>Creality MK8</li>
<li>Creality Spider V3</li>
<li>Creality Spider V3 + Volcano nozzle or Meltzone extender</li>
<li>DropEffect neXtG HF</li>
<li>DropEffect neXtG UHF</li>
<li>E3D V6</li>
<li>E3D V6 Volcano</li>
<li>E3D Revo Voron</li>
<li>Goliath air</li>
<li>Phaetus Dragon SF</li>
<li>Phaetus Dragon HF</li>
<li>Phaetus Dragon 2 HF</li>
<li>Phaetus Dragon 2 UHF</li>
<li>Phaetus Dragonfly BMS</li>
<li>Phaetus Rapido (2) HF</li>
<li>Phaetus Rapido (2) UHF</li>
<li>TriangleLab ACE</li>
<li>TriangleLab ACE+</li>
</ul>
</details>

<details>
    <summary><h4 style="display:inline-block;margin-left:1.5em;color:#FF0000;font-weight:bold"> WARNING! </h4></summary>
<p>Hotends with E3D groove mount heatsink are not generaly recommended with the E3NG toolhead. The reason is the long heatsink which doesn't properly fit and because of it the heatsink cooling is not optimal. I couldn't test it myself yet but i believe it may cause clogs due to heatcreep in some situations.</p>
<p>If you are willing to test it, please let me know.</p>
<p>Instead of the E3D groove mount, I recommend using the V6DM heatsink by TriangleLab which is a direct replacement and it uses a 4 screw mount.</p>
</details>

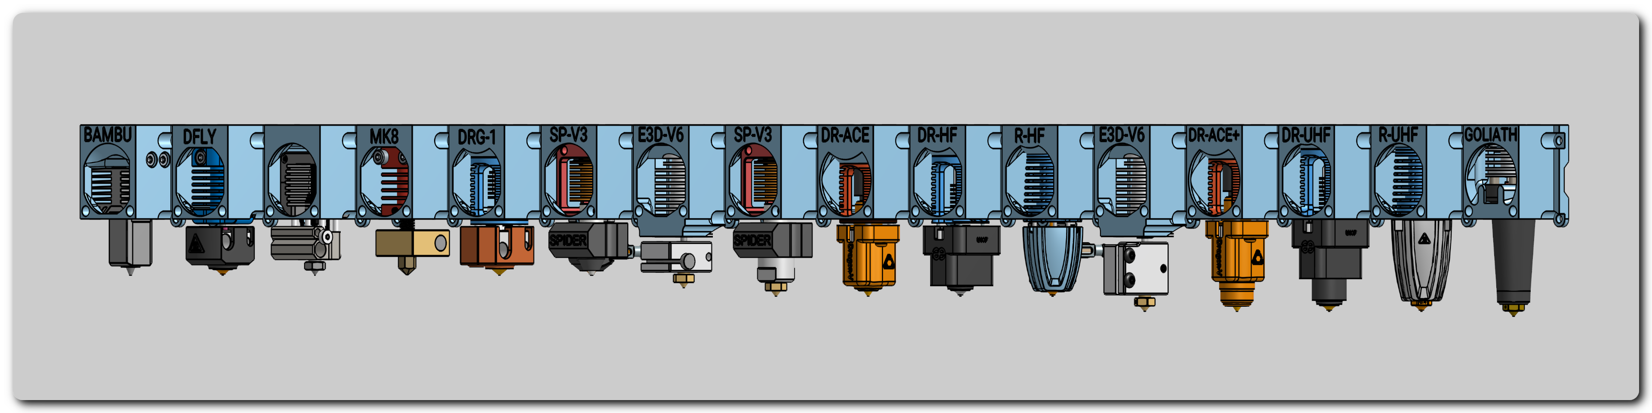
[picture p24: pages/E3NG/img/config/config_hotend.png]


#### EXTRUDER
- Bowden - adapter plate for different bowden connectors - bowden clip / ECAS04 / M6 thread (used on stock Ender extruder) / 1/8' thread (used on stock Ender hotend) / SpiderV3 coupler / Phaetus groove mount adapter
- Original design extruders - adapter plates with the most common mounts to fit the majority of direct drive extruders.
- Integrated - direct drive extruders with integration into the toolhead mount. Makes mounting the extruder more secure and rigid while still being easy to swap.



#### PART COOLING
- 2 x 4010 - RECOMMENDED - compact and solid option with higher RPM fans - great option for most of the users.
- 2 x 4020 - step up in performance from the previous 4010 fans.
- 2 x 5015 - even more air.
- CPAP - the best choice for extreme cooling and lightweight toolhead, although you can always add auxiliary fans too.

<details>
    <summary><h4 style="display:inline-block;margin-left:1.5em;color:#FF0000;font-weight:bold"> WARNING! </h4></summary>
<p>Because of the 5015 blower fan size, combination with a very short hotend results in a bit more restrictive fan duct design and as a result using 4020 fans might be a better choice. With longer hotends, the 5015 fanduct design is fine.</p>
</details>



#### BED PROBE
Choose the right bed probe for you.
- KlickyPCB - RECOMMENDED cheap option with good reliability.
- BDSensor - RECOMMENDED performance option - it is recommended more than Beacon scanner as it doesn't have the "no metal" zone that is forcing Beacon to be further from the nozzle because of the lower LM8LUU. BDSensor is currently more complicated to install but Klipper integration is in the works.

<details>
    <summary><h4 style="display:inline-block;margin-left:1.5em;color:#5ca33c;font-weight:bold"> COMPATIBLE PROBES </h4></summary>
<p>Listed probes were directly tested in the CAD design or/and in real life and have a specific mount, so it is verified they can be used.</p>
<ul style="margin-left:2em;font-size:14px">
<li>BDsensor</li>
<li>Beacon scanner</li>
<li>BIQU microprobe</li>
<li>BLTouch</li>
<li>BTT Eddy</li>
<li>CR Touch</li>
<li>Klicky probe</li>
<li>KlickyPCB</li>
<li>P.I.N.D.A. / SuperPINDA</li>
</ul>
</details>

<details>
    <summary><h4 style="display:inline-block;margin-left:1.5em;color:#FF0000;font-weight:bold"> WARNING! </h4></summary>
<p>When building version with three Z linear rods and using some of the directly mounted probes (BDsensor, Beacon scanner, BTT Eddy, P.I.N.D.A.) with a longer hotend, keep in mind, there can be a conflict between the rear Z rod and the probe. In normal operation it is not an issue becauce it is only a small zone outside the print and homing area but can happen during maintenance or when not set properly.</p>
<p>Keep this in mind so you don't brake your probe mount or even the probe.</p>
</details>



#### ACCESSORIES
- Cable guide - RECOMMENDED for keeping the toolhead wiring clean and safe.
- Breakout board - cheap DIY alternative to toolhead PCB boards using female JST XH connectors and wires directly soldered to them. 5x2pin and 1x3pin
- Accelerometer mount - it is recommended to use nozzle mounted for your accelerometer but this option is easier/faster to use. It has KUSBA as well as ADXL345 mount pattern.



---
# MODS / UPGRADES
{: .text-center }

#### STEPPER COOLING
Optional active cooling for AB steppers using 4020 axial fans. It is simple yet very effective solution that keeps your steppers cool allowing you to increase the run current and print faster.



#### FRAME BRACES
Recommended if you are using legacy version of the frame without the enclosure. It adds a bit more rigidity to the frame but other frame variants are rigid enough and the enclosure is even superior in that regard.



#### HANDLES
Handles - RECOMMENDED - to have a good grip on the printer. Handles are automatically added if you select enclosure.



#### LED LIGHTS
- Frame LEDs - RECOMMENDED - LED strips mounted on the frame in the nozzle height to better see the prints.
- Enclosure LEDs - RECOMMENDED - LED strips mounted on the upper edge of the enclosure to light up the inside of the printer.



#### AUX COOLING
Auxiliary side cooling using 12032 fans blowing air over the build plate from both sides. For more powerful cooling for your prints.



#### BED WIRING - WAGO 221
For running bed heater cables from your board into the connectors mounted on the bed carriage. It helps with serviceability as you can remove the bed completely without removing all the cables. It uses Wago 221 connectors for the heater wiring and JST XH connectors for the thermistor and/or under bed fan.
- DC BED - for DC - usually 24V bed heaters.
- AC BED - for AC bed heaters including connector for the ground wire.



#### UNDER BED FAN
RECOMMENDED if you install enclosure. Helps circulating the air inside the chamber and heating it faster and more evenly by sucking the warm air from below the heated bed and blowing it down. It also helps moving/mixing air in the entire enclosure making it more evenly heated.



#### AUTO Z - VORON
Original Voron design for Auto-Z offset with using "Sexbolt" nozzle endstop.



continue to:
{: .text-right .lh-0 .pt-8 }

[SOURCING PARTS]{: .btn .fs-6 .fw-300 .text-yellow-300 }
{: .text-right }

[CONFIGURATOR DOWNLOAD]: ../../assets/docs/E3NG_BOM_250217.xlsm
[BASE BUILD]: https://rh3d.xyz/E3NG_v1_2/advanced/config#base-build
[TOOLHEAD]: https://rh3d.xyz/E3NG_v1_2/advanced/config#toolhead
[MODS / UPGRADES]: https://rh3d.xyz/E3NG_v1_2/advanced/config#mods--upgrades
[SOURCING PARTS]: https://rh3d.xyz/E3NG_v1_2/advanced/sourcing_parts

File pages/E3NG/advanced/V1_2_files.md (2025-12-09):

---
title: Files
layout: default
parent: v1.2 - (advanced)
grand_parent: E3NG v1.2
has_children: false
nav_order: 40
description: "Download STL files and organize your E3NG v1.2 CoreXY build. Use the RH3D configurator for accurate part lists and explore remix mods on Printables or Discord."
permalink: /E3NG_v1_2/advanced/files
---
# FILES
{: .text-center }

All the printable files are hosted on printables, organised into folder structure based on the part location. It is the only official source of printable files and is always up to date with all the changes mentioned in the changelog.
{: .text-center }

[PRINTABLES]{: .btn .fs-7 .fw-300 .mt-6 .mb-8 .text-yellow-300 }
{: .text-center }

The CAD assembly files are currently an extra bonus for supporters and available through a small purchase on Ko-Fi page.
{: .text-center }

<div>
<script type='text/javascript' src='https://storage.ko-fi.com/cdn/widget/Widget_2.js'></script><script type='text/javascript'>kofiwidget2.init('Ko-fi', '#28b5e0', 's/f1be48e43a');kofiwidget2.draw();</script> 
</div>
{: .text-center .mt-6 .mb-8 }

---
To better understand and organise your files, it is highly recommended to go through the configurator carefully and print out your final list of printed parts. It includes the required quantity and the recommended color to print your parts.

---
#### MODS / REMIXES

*It’s highly recommended to begin with the stock project to follow a clear path, receive accurate and complete instructions, and work from reliable lists. Once you're familiar with the build, you can start exploring user mods if you wish.*

*Most remixes and modifications are available on [Printables remixes], though you’ll find additional ones on the Discord server. There are also many [remixes for the beta] version, most of which remain compatible.*

continue to:
{: .text-right .lh-0 .pt-8 }

[BUILD GUIDE]{: .btn .fs-6 .fw-300 .text-yellow-300 }
{: .text-right }

[BUILD GUIDE]: https://rh3d.xyz/E3NG_v1_2/advanced/build_guide
[PRINTABLES]: https://www.printables.com/en/model/922401/files
[Printables remixes]: https://www.printables.com/en/model/922401/remixes
[remixes for the beta]: https://www.printables.com/en/model/469280/remixes

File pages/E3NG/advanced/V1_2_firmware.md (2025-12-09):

---
title: Firmware
layout: default
parent: v1.2 - (advanced)
grand_parent: E3NG v1.2
has_children: false
nav_order: 60
description: "Firmware support for advanced E3NG v1.2 CoreXY builds. Until available, follow the v1.2S guide for Klipper or Marlin configs and compatible controller boards."
permalink: /E3NG_v1_2/advanced/firmware
---
# FIRMWARE
{: .text-center }

Please refer to the Firmware section for the E3NG v1.2S for now.
{: .text-center }

# [E3NG v1.2S firmware]
{: .text-center }

continue to:
{: .text-right .lh-0 .pt-8 }

[FINAL SETUP]{: .btn .fs-6 .fw-300 .text-yellow-300 }
{: .text-right }

[E3NG v1.2S firmware]: https://rh3d.xyz/E3NG_v1_2/standard/firmware
[FINAL SETUP]: https://rh3d.xyz/E3NG_v1_2/final_setup

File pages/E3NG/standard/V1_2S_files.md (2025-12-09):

---
title: Files
layout: default
parent: v1.2S - (standard)
grand_parent: E3NG v1.2
has_children: false
nav_order: 30
description: "Download and organize STL files for E3NG v1.2S CoreXY builds. Learn part naming formats, color coding, quantity hints, and printer compatibility details."
permalink: /E3NG_v1_2/standard/files
---
# FILES
{: .text-center }

To download the STL files package, follow the link below and navigate to the bottom of the page to download: OTHER FILES - **E3NG_v1.2S.zip**.
{: .text-center }

[PRINTABLES]{: .btn .fs-7 .fw-300 .mt-6 .mb-8 .text-yellow-300 }
{: .text-center }

---
Before printing any files, let's take a quick look at the folder and filename structure.

The folder structure is intentionally simple, designed to help you organize parts based on their placement on the printer.

The filenames follow a consistent format based on the part’s position, but pay close attention to the end of each name. Every file includes a small note in brackets, and some may also contain additional information such as size or variant details.

### STANDART FILE NAMING
A typical filename looks like this: `filename_[M_2].stl`. The bracket contains two important pieces of information:

#### COLOR
 - `M` = main color
 - `A` = accent color
 - `X` = assembly-use only, part is not used on the final printer, use any color

#### QUANTITY
 - A number indicates how many pieces to print
 - `X` = optional, *you'll need to decide based on your configuration. If you are not sure, it is recommended to view the build guide to become familiar with the part function, for example:*
   - `E3` = needed only for Ender 3 as a base printer, *eg. `frame_bottom_fix_left_E3_[M-X].stl`*
   - `E3V2` = needed only for Ender 3 V2, *eg. `electronics_power_switch_front_E3V2_[M-X].stl`*
   - Also present on toolhead parts.

### OPTIONAL FILE ATTRIBUTES
Some files include additional descriptors before the bracket which help you decide the quantity needed if `X` is specified in the bracket, like this: `filename-S_[A_X].stl`.

#### SIZE
 - `S` = small
 - `M` = medium
 - `L` = large

*This primarily applies to toolhead parts. Choose the hotend mount based on the hotend you’re using, then print the other parts (cooling ducts, probe mounts, etc.) using the same size designation.*

Example: `toolhead_hotend_bambulab-S_[A-X].stl`
  - indicates size `S`.
    - *Use the same size prefix for related parts - `toolhead_fanduct_4010_S_[A-X].stl` and `toolhead_probe_....._S_[A-X].stl`*
  - If a probe file has no size specified, it's considered universal.

#### PRINTER VARIANT
 - `E3` = Creality Ender 3 used as a base printer for conversion.
 - `E3V2` = Creality Ender 3 V2 used as a base printer for conversion.

---
#### MODS / REMIXES

*It’s highly recommended to begin with the stock project to follow a clear path, receive accurate and complete instructions, and work from reliable lists. Once you're familiar with the build, you can start exploring user mods if you wish.*

*Most remixes and modifications are available on [Printables remixes], though you’ll find additional ones on the Discord server. There are also many [remixes for the beta] version, most of which remain compatible.*

continue to:
{: .text-right .lh-0 .pt-8 }

[BUILD GUIDE]{: .btn .fs-6 .fw-300 .text-yellow-300 }
{: .text-right }

[PRINTABLES]: https://www.printables.com/en/model/922401/files
[BUILD GUIDE]: https://rh3d.xyz/E3NG_v1_2/standard/build_guide
[Printables remixes]: https://www.printables.com/en/model/922401/remixes
[remixes for the beta]: https://www.printables.com/en/model/469280/remixes

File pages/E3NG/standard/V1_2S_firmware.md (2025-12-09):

---
title: Firmware
layout: default
parent: v1.2S - (standard)
grand_parent: E3NG v1.2
has_children: false
nav_order: 50
description: "Set up Klipper or Marlin firmware for your E3NG v1.2S CoreXY build. Get configs, docs, and board compatibility details to prepare your Ender 3 conversion."
permalink: /E3NG_v1_2/standard/firmware
---
# FIRMWARE
{: .text-center }

To finally run the printer, we need to set up the Firmware.

*To learn how to install it, it is recommended to search their official websites along with the motherboard manufacturer GitHub (if available) for the most up to date information.*

*It is also extremely helpful to follow other available guides on YouTube or some discussion websites.*

---
# Klipper FW

*For extremely fast printing, more advanced tuning and high-end features.* **[Klipper FW]**

## BigTreeTech SKR mini E3 V2
{: .text-center }
[download printer.cfg](https://github.com/RH3D/E3NG/blob/main/firmware/Klipper/v1.2S/E3NG_v1.2S_SKR3miniE3_V2_printer.cfg) | [official BTT documentation](https://github.com/bigtreetech/BIGTREETECH-SKR-mini-E3) | [BUY](https://s.click.aliexpress.com/e/_DCIOnMr)
{: .text-center }

## BigTreeTech SKR 3 EZ
{: .text-center }
[download printer.cfg](https://github.com/RH3D/E3NG/blob/main/firmware/Klipper/v1.2S/E3NG_v1.2S_SKR3EZ_printer.cfg) | [official BTT documentation](https://github.com/bigtreetech/SKR-3) | [BUY](https://s.click.aliexpress.com/e/_oDu0HPc)
{: .text-center }

## BigTreeTech Octopus v1.0 (and v1.1)
{: .text-center }
[download printer.cfg](https://github.com/RH3D/E3NG/blob/main/firmware/Klipper/v1.2S/E3NG_v1.2S_Octopus_v1.1_printer.cfg) | [official BTT documentation](https://github.com/bigtreetech/BIGTREETECH-OCTOPUS-V1.0) | [BUY](https://s.click.aliexpress.com/e/_Dd8mCyj)
{: .text-center }

---
# Marlin FW

*For the printer simplicity and saving some resources while still being able to print pretty fast and taking advantage of most of the advanced features.* **[Marlin FW]**

## BigTreeTech SKR mini E3 V2
{: .text-center }
[download FW files](https://github.com/RH3D/E3NG/blob/main/firmware/Marlin/v1.2S/E3NG_M2.1.x_config_SKRminiE3v2.zip) | [official BTT documentation](https://github.com/bigtreetech/BIGTREETECH-SKR-mini-E3) | [BUY](https://s.click.aliexpress.com/e/_DCIOnMr)
{: .text-center }

## BigTreeTech SKR 3 EZ
{: .text-center }
[download FW files](https://github.com/RH3D/E3NG/blob/main/firmware/Marlin/v1.2S/E3NG_M2.1.x_config_SKR3EZ.zip) | [official BTT documentation](https://github.com/bigtreetech/SKR-3) | [BUY](https://s.click.aliexpress.com/e/_oDu0HPc)
{: .text-center }

continue to:
{: .text-right .lh-0 .pt-8 }

[FINAL SETUP]{: .btn .fs-6 .fw-300 .text-yellow-300 }
{: .text-right }

[Klipper FW]: https://www.klipper3d.org/
[Marlin FW]: https://marlinfw.org/
[FINAL SETUP]: https://rh3d.xyz/E3NG_v1_2/final_setup

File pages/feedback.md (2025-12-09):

---
#title: Feedback ✉️
layout: default
nav_order: 100
permalink: /feedback.html
---
# FEEDBACK
{: .text-center }

If you want to:
- Give any feedback on the project or related things.
- Help sorting out issues you have found.
- Help supporting the project by using affiliate links that are not in the BOM.
- Contact RH3D about a possible cooperation or want to be selling parts/kits specific to the project.

Please use the form in the link below:
{: .text-center .lh-1 .pt-8 }

[FEEDBACK FORM]{: .btn .fs-6 .fw-300 .text-yellow-300 }
{: .text-center }
*Created with Google Forms.*
{: .text-center .fs-3 .mt-0 .fw-300 }

[FEEDBACK FORM]: https://forms.gle/o5UT37fGMugg6jLb9

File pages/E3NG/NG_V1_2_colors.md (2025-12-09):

---
title: Color scheme
layout: default
parent: E3NG v1.2
#has_children: true
nav_order: 40
description: "Customize your E3NG v1.2 build with RH3D’s color scheme tool. Preview accent and main colors in real-time for a personalized CoreXY printer design."
permalink: /E3NG_v1_2/color_scheme
---
<html lang="cs">
<head>
    <meta charset="UTF-8">
    <meta name="viewport" content="width=device-width, initial-scale=1.0">
    <title>E3NG Color scheme helper</title>
    <style>
        body {
            /*display: flex;
            flex-direction: column;*/
            align-items: center;
            justify-content: center;
            height: 100vh;
            margin: 0;
        }
        .container {
            position: relative;
            width: 100%; /* Nastavení pevné šířky */
            height: 600px; /* Nastavení pevné výšky */
        }
        .background-image, .foreground-image, .foreground-image-2, .overlay-image {
            position: absolute;
            top: 0;
            left: 0;
            width: 100%;
            height: 100%;
            object-fit: contain; /* Zachování poměru stran */
        }
        .background-image {
            z-index: 1;
        }
        .foreground-image {
            z-index: 2;
        }
        .foreground-image-2 {
            z-index: 3;
            filter: saturate(0%) brightness(40%);
        }
        .overlay-image {
            z-index: 4; /* Nový obrázek překrývající ostatní */
        }
        .slider-container {
            margin: 10px 0;
            display: flex;
            align-items: center;
        }
        .slider {
            width: 100%;
            margin-left: 10px;
        }
        .number-input {
            width: 40px;
            margin-left: 10px;
        }
        .sliders-group {
            display: flex;
            justify-content: space-between;
            width: 100%;
            margin-top: 20px; /* Přidání mezery mezi obrázkem a posuvníky */
        }
        .sliders-column {
            display: flex;
            flex-direction: column;
            align-items: right;
            width: 47%; /* Zmenšení šířky sloupců */
        }
    </style>
</head>
<body>
    <div class="container">
        BG
        AC
        MC
        OL
    </div>
    <div class="sliders-group">
        <div class="sliders-column">
            <h2>ACCENT COLOR</h2>
            <div class="slider-container">
                <label for="brightness">BRI</label>
                <input type="number" id="brightness-number" class="number-input" min="0" max="100" value="50">
                <input type="range" id="brightness" class="slider" min="0" max="100" value="50">
            </div>
            <div class="slider-container">
                <label for="saturation">SAT</label>
                <input type="number" id="saturation-number" class="number-input" min="0" max="100" value="50">
                <input type="range" id="saturation" class="slider" min="0" max="100" value="50">
            </div>
            <div class="slider-container">
                <label for="hue">HUE</label>
                <input type="number" id="hue-number" class="number-input" min="0" max="100" value="0">
                <input type="range" id="hue" class="slider" min="0" max="100" value="0">
            </div>
        </div>
        <div class="sliders-column">
            <h2>MAIN COLOR</h2>
            <div class="slider-container">
                <label for="brightness-2">BRI</label>
                <input type="number" id="brightness-number-2" class="number-input" min="0" max="100" value="20">
                <input type="range" id="brightness-2" class="slider" min="0" max="100" value="20">
            </div>
            <div class="slider-container">
                <label for="saturation-2">SAT</label>
                <input type="number" id="saturation-number-2" class="number-input" min="0" max="100" value="0">
                <input type="range" id="saturation-2" class="slider" min="0" max="100" value="0">
            </div>
            <div class="slider-container">
                <label for="hue-2">HUE</label>
                <input type="number" id="hue-number-2" class="number-input" min="0" max="100" value="0">
                <input type="range" id="hue-2" class="slider" min="0" max="100" value="0">
            </div>
        </div>
    </div>

    <script>
        const foregroundImage = document.getElementById('foreground-image');
        const brightnessSlider = document.getElementById('brightness');
        const brightnessNumber = document.getElementById('brightness-number');
        const saturationSlider = document.getElementById('saturation');
        const saturationNumber = document.getElementById('saturation-number');
        const hueSlider = document.getElementById('hue');
        const hueNumber = document.getElementById('hue-number');

        const foregroundImage2 = document.getElementById('foreground-image-2');
        const brightnessSlider2 = document.getElementById('brightness-2');
        const brightnessNumber2 = document.getElementById('brightness-number-2');
        const saturationSlider2 = document.getElementById('saturation-2');
        const saturationNumber2 = document.getElementById('saturation-number-2');
        const hueSlider2 = document.getElementById('hue-2');
        const hueNumber2 = document.getElementById('hue-number-2');

        const overlayImage = document.getElementById('overlay-image');

        function updateImage(image, brightness, saturation, hue) {
            image.style.filter = `brightness(${brightness * 2}%) saturate(${saturation * 2}%) hue-rotate(${hue * 3.6}deg)`;
        }

        function syncSlidersAndNumbers(slider, number, image, type, otherSliders) {
            slider.addEventListener('input', () => {
                number.value = slider.value;
                if (type === 'brightness') {
                    updateImage(image, slider.value, otherSliders.saturation.value, otherSliders.hue.value);
                } else if (type === 'saturation') {
                    updateImage(image, otherSliders.brightness.value, slider.value, otherSliders.hue.value);
                } else if (type === 'hue') {
                    updateImage(image, otherSliders.brightness.value, otherSliders.saturation.value, slider.value);
                }
            });
            number.addEventListener('input', () => {
                slider.value = number.value;
                if (type === 'brightness') {
                    updateImage(image, number.value, otherSliders.saturation.value, otherSliders.hue.value);
                } else if (type === 'saturation') {
                    updateImage(image, otherSliders.brightness.value, number.value, otherSliders.hue.value);
                } else if (type === 'hue') {
                    updateImage(image, otherSliders.brightness.value, otherSliders.saturation.value, number.value);
                }
            });
        }

        syncSlidersAndNumbers(brightnessSlider, brightnessNumber, foregroundImage, 'brightness', {saturation: saturationSlider, hue: hueSlider});
        syncSlidersAndNumbers(saturationSlider, saturationNumber, foregroundImage, 'saturation', {brightness: brightnessSlider, hue: hueSlider});
        syncSlidersAndNumbers(hueSlider, hueNumber, foregroundImage, 'hue', {brightness: brightnessSlider, saturation: saturationSlider});

        syncSlidersAndNumbers(brightnessSlider2, brightnessNumber2, foregroundImage2, 'brightness', {saturation: saturationSlider2, hue: hueSlider2});
        syncSlidersAndNumbers(saturationSlider2, saturationNumber2, foregroundImage2, 'saturation', {brightness: brightnessSlider2, hue: hueSlider2});
        syncSlidersAndNumbers(hueSlider2, hueNumber2, foregroundImage2, 'hue', {brightness: brightnessSlider2, saturation: saturationSlider2});
    </script>
</body>
</html>

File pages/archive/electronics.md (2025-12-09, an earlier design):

---
#title: Printer electronics
layout: default
has_children: true
nav_order: 5
permalink: /electronics.html
---
# PRINTER ELECTRONICS
{: .text-center }

{: .note }
Please, follow the updated link: [E3NG v1.2S FIRMWARE]

[E3NG v1.2S FIRMWARE]: https://rh3d.xyz/E3NG_v1_2/standard/firmware

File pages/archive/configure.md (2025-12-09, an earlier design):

---
#title: Printer configuration
layout: default
parent: Into the project
#has_children: true
nav_order: 1
permalink: /configure.html
---

# PRINTER CONFIGURATION
{: .text-center }
[CONFIGURATOR DOWNLOAD]{: .btn .fs-6 .fw-300 .mt-8 .text-yellow-300 }
{: .text-center }
_last updated: 2024.10.25 10:00 (UTC +02:00)_{: .fs-3 .mt-0 .fw-300 }
{: .text-center }

<details>
    <summary><h4 style="display:inline-block;margin-left:1.5em"> CHANGELOG </h4></summary>
<p>2024.10.25 - Added Funssor kits / Updated all current prices in BOM / fixed BTT Eddy printed mounts</p>
<p>2024.08.19 - Added Fushi bearing and shaft kit / changed RDBB linear rods for Fushi linear rods incl 12x320 mm / fixed link for LED strips</p>
<p>2024.08.15 - Initial public release</p>
</details>

*You will be guided through all the steps in the configurator and you will get helpful and detailed information for all the available options. This page aims to explain differences between options in more detail, but their effect on the BOM or required parts will show up in the configurator file.*

<details>
    <summary><h4 style="display:inline-block;margin-left:1.5em"> WHAT IS THE CONFIGURATOR, HOW DOES IT WORK? </h4></summary>
<p>CONFIGURATOR is an all in one interactive spreadsheet that includes Configurator, Bill of material, Printed parts and list of verified/approved kits.
The Configurator will, based on your setup, automatically calculate the right quantities in the Bill of Material, show you the right parts to print and even the estimated cost of the BOM and the amount of filament needed. There are two macros included to show/hide unused parts to better organise the table but they are not neccessary to run if you have concerns.</p>
<p>BOM also includes links to buy parts - links are affiliate and help by a small amount to the project with no added cost to you.</p>
<p>The default values are the recommended ones for a good price-performance ratio. Of course, otherwise I would recommend to build the best performing version.</p>
</details>

The configuration is divided into three sections:

[BASE BUILD]{: .btn .fs-5 .fw-300 .text-yellow-300 .mr-7 .px-6 }
[TOOLHEAD]{: .btn .fs-5 .fw-300 .text-yellow-300 .mr-7 .px-6 }
[MODS / UPGRADES]{: .btn .fs-5 .fw-300 .text-yellow-300 .px-6 }
{: .text-center }

{: .note }
All the pictures bellow are higher resolution, so you can zoom in or right click - Open image in new tab/window - to view it in more detail.

# BASE BUILD
{: .text-center }

#### BASE PRINTER
Supported and tested printers for the conversion. Compatibility with other printers will be verified and tested over time so if you decide to use a different one for the conversion and want to help with the implementation, please give me feedback. There are also dimensions for the aluminium extrusions in the BOM, so you can check the compatibility yourself or even build the printer from scratch.
- Creality Ender 3 - has 2040 x 330 mm extrusion for Y axis - printed spacer is used.
- Creality Ender 3 Pro - default, has 4040 x 350 mm extrusion for Y axis.
- Creality Ender 3 V2 - some have shorter 4040 extrusion for Y axis - printed spacer is used.



#### ENCLOSURE
Choosing to enclose the printer or not. V2 style enclosure is better designed and simpler while also adding to the frame rigidity. For the best experience, recommended polycarbonate panels are 4mm thick + 5mm for the front door. Rear electronics cover can be 3mm.



#### FRAME
- Printed verticals - legacy version where you don't need to buy extra extrusions. Depending on your filament and market prices, it can also be the cheapest option.
- 2040 upgrade - RECOMMENDED - first stage upgrade with additional V-slot extrusion. Adds rigidity to the frame and reduces printing parts. Requires drilling and tapping.
- Ultimate frame - all you need for the best performance, adds two more extrusions to the front. Requires more driling and tapping.

<details>
    <summary><h4 style="display:inline-block;margin-left:1.5em;color:#0096FF;font-weight:bold"> TIP </h4></summary>
<p>For Ultimate frame, you are also buying 300 mm V-slot extrusions which fit into 310 mm space with printed spacers for ease of buying the common size. If you are ordering custom extrusions or cutting them yourself, you can instead use 310 mm extrusions without spacers.</p>
</details>



#### Z AXIS RODS
- 2x12 mm rod - legacy version - simple setup that works well enough if your leadscrews are not extremely bent, it also saves few dollars.
- 3x12 mm rod - RECOMMENDED - uses linear rod at the rear leadscrew, makes the bed carriage more stable. This is required if you plan to use tilting bed _(once it is released)_.

<details>
    <summary><h4 style="display:inline-block;margin-left:1.5em;color:#0096FF;font-weight:bold"> TIP </h4></summary>
<p>For 3x12 mm rod option, the rear rod is 320 mm long to preserve the toolhead motion over the entire area. While this is not a common size, the BOM lists some options but if you cannot buy 320 mm version and you are unable to cut a 350 mm rod, the design also allows to use 300 mm rod but then it is only sunk in by 7,5 mm on each side. While this will still work, I recommend using a 320 mm option for better reliability.</p>
</details>



#### BED CARRIAGE
- Printed - although it works, it is not recommended. It is a backup option for people who cannot use one of the others.
- Stock E3 bed carriage - RECOMMENDED - reuse the stock Ender's bed carriage. Requires drilling and tapping.
- Metal carriage - cut with laser od water, most rigid option, if you want to get the best out of your printer.
- _Z-tilt bed - in development_



#### Z WOBBLE COMPENSATION
- None - no Z wobble compensation, T8/8 nuts mounted directly.
- Flexi joint - RECOMMENDED - printed flexible inserts that compensate leadscrew runout.
- WobbleX - more efficient solution by MirageC, but it reduces the max Z by around 22 mm.



#### Z AXIS DRIVE
- 1 stepper - RECOMMENDED - more foolproof and simple solution with one stepper and long belt driving all 3 leadscrews, also cheaper.
- 3 steppers - for individualy driven leadscrews and Z-tilt option. This is required if you plan to use tilting bed _(once it is released)_, but currently this option isn't recommended as there is no compliant mechanism in the bed carriage.

<details>
    <summary><h4 style="display:inline-block;margin-left:1.5em;color:#FF0000;font-weight:bold"> WARNING! </h4></summary>
<p>When using a 3 stepper option with a bed carriage that isn't properly designed for tilt, there is a significant chance of excessive load on LM12UU bearings and leadscrews which can result in binding, increased friction and faster wear of components or worse print quality if your bed is not aligned properly.</p>
<p>If you select this option, be very careful, make sure your bed is aligned well resulting in a minimal tilt of the bed carriage (not only the bed plate) and check the function/alignment regularly.</p>
<p>Do at your own responsibility, you have been warned.</p>
</details>



#### LEADSCREW PULLEYS
- Printed - legacy version - cheap and simple option but for good performance it is important to verify that there is no ovality in pulleys and the print is precise.
- Aluminium - RECOMMENDED - precise aluminium pulley equals precise leadscrew rotation.



#### PSU THICKNESS
- 30 mm - thinner Meanwell PSU used in Ender 3 Pro and in some Ender 3 V2
- 50 mm - thicker PSU used in Ender 3 and in some Ender 3 V2



#### BOARD MOUNT
Currently there are setups for only few motherboards but more will be directly supported in the future. The supported board has DIN rail mount along with cooling fan holder and there is also a FW setup available. But being the boards mounted on DIN rails, it is easy to use any other board.
- BTT SKR mini E3 v2
- BTT SKR3EZ
- BTT Octopus
- Other - includes universal cooling fan housing mounted directly on the rear panel.

<details>
    <summary><h4 style="display:inline-block;margin-left:1.5em;color:#0096FF;font-weight:bold"> TIP </h4></summary>
<p>Apart from the main board mount you may also need mounts for other electronics. Have a look at EXTRAS folder, there are Raspberry Pi, SSR, 5V PSU and other mounts.</p>
</details>



# TOOLHEAD
{: .text-center }
Toolhead is put together with separate parts for mounting each of the components which makes it super easy to alternate between different types of hardware or doing a maintenance.



#### HOTEND
Select the hotend you want to use, it is generaly recommended to use hotend with higher flow.

<details>
    <summary><h4 style="display:inline-block;margin-left:1.5em;color:#5ca33c;font-weight:bold"> COMPATIBLE HOTENDS </h4></summary>
<p>Listed hotends were directly tested in the CAD design or/and in real life and have a specific mount, so it is verified they can be used. Some of the mount styles are widely used so the real compatibility list will be even bigger.</p>
<ul style="margin-left:2em;font-size:14px">
<li>BambuLab hotends</li>
<li>Creality MK8</li>
<li>Creality Spider V3</li>
<li>Creality Spider V3 + Volcano nozzle or Meltzone extender</li>
<li>DropEffect neXtG HF</li>
<li>DropEffect neXtG UHF</li>
<li>E3D V6</li>
<li>E3D V6 Volcano</li>
<li>E3D Revo Voron</li>
<li>Goliath air</li>
<li>Phaetus Dragon SF</li>
<li>Phaetus Dragon HF</li>
<li>Phaetus Dragon 2 HF</li>
<li>Phaetus Dragon 2 UHF</li>
<li>Phaetus Dragonfly BMS</li>
<li>Phaetus Rapido (2) HF</li>
<li>Phaetus Rapido (2) UHF</li>
<li>TriangleLab ACE</li>
<li>TriangleLab ACE+</li>
</ul>
</details>

<details>
    <summary><h4 style="display:inline-block;margin-left:1.5em;color:#FF0000;font-weight:bold"> WARNING! </h4></summary>
<p>Hotends with E3D groove mount heatsink are not generaly recommended with the E3NG toolhead. The reason is the long heatsink which doesn't properly fit and because of it the heatsink cooling is not optimal. I couldn't test it myself yet but i believe it may cause clogs due to heatcreep in some situations.</p>
<p>If you are willing to test it, please let me know.</p>
<p>Instead of the E3D groove mount, I recommend using the V6DM heatsink by TriangleLab which is a direct replacement and it uses a 4 screw mount.</p>
</details>



#### EXTRUDER
- Bowden - adapter plate for different bowden connectors - bowden clip / ECAS04 / M6 thread (used on stock Ender extruder) / 1/8' thread (used on stock Ender hotend) / SpiderV3 coupler / Phaetus groove mount adapter
- Original design extruders - adapter plates with the most common mounts to fit the majority of direct drive extruders.
- Integrated - direct drive extruders with integration into the toolhead mount. Makes mounting the extruder more secure and rigid while still being easy to swap.



#### PART COOLING
- 2 x 4010 - RECOMMENDED - compact and solid option with higher RPM fans - great option for most of the users.
- 2 x 4020 - step up in performance from the previous 4010 fans.
- 2 x 5015 - even more air.
- CPAP - the best choice for extreme cooling and lightweight toolhead, although you can always add auxiliary fans too.

<details>
    <summary><h4 style="display:inline-block;margin-left:1.5em;color:#FF0000;font-weight:bold"> WARNING! </h4></summary>
<p>Because of the 5015 blower fan size, combination with a very short hotend results in a bit more restrictive fan duct design and as a result using 4020 fans might be a better choice. With longer hotends, the 5015 fanduct design is fine.</p>
</details>



#### BED PROBE
Choose the right bed probe for you.
- KlickyPCB - RECOMMENDED cheap option with good reliability.
- BDSensor - RECOMMENDED performance option - it is recommended more than Beacon scanner as it doesn't have the "no metal" zone that is forcing Beacon to be further from the nozzle because of the lower LM8LUU. BDSensor is currently more complicated to install but Klipper integration is in the works.

<details>
    <summary><h4 style="display:inline-block;margin-left:1.5em;color:#5ca33c;font-weight:bold"> COMPATIBLE PROBES </h4></summary>
<p>Listed probes were directly tested in the CAD design or/and in real life and have a specific mount, so it is verified they can be used.</p>
<ul style="margin-left:2em;font-size:14px">
<li>BDsensor</li>
<li>Beacon scanner</li>
<li>BIQU microprobe</li>
<li>BLTouch</li>
<li>BTT Eddy</li>
<li>CR Touch</li>
<li>Klicky probe</li>
<li>KlickyPCB</li>
<li>P.I.N.D.A. / SuperPINDA</li>
</ul>
</details>

<details>
    <summary><h4 style="display:inline-block;margin-left:1.5em;color:#FF0000;font-weight:bold"> WARNING! </h4></summary>
<p>When building version with three Z linear rods and using some of the directly mounted probes (BDsensor, Beacon scanner, BTT Eddy, P.I.N.D.A.) with a longer hotend, keep in mind, there can be a conflict between the rear Z rod and the probe. In normal operation it is not an issue becauce it is only a small zone outside the print and homing area but can happen during maintenance or when not set properly.</p>
<p>Keep this in mind so you don't brake your probe mount or even the probe.</p>
</details>



#### ACCESSORIES
- Cable guide - RECOMMENDED for keeping the toolhead wiring clean and safe.
- Breakout board - cheap DIY alternative to toolhead PCB boards using female JST XH connectors and wires directly soldered to them. 5x2pin and 1x3pin
- Accelerometer mount - it is recommended to use nozzle mounted for your accelerometer but this option is easier/faster to use. It has KUSBA as well as ADXL345 mount pattern.



# MODS / UPGRADES
{: .text-center }

#### STEPPER COOLING
RECOMMENDED - optional active cooling for AB steppers using 4020 axial fans. It is simple yet very effective solution that keeps your steppers cool allowing you to increase the run current and print faster.



#### FRAME BRACES
Recommended if you are using legacy version of the frame without the enclosure. It adds a bit more rigidity to the frame but other frame variants are rigid enough and the enclosure is even superior in that regard.



#### HANDLES
Handles - RECOMMENDED - to have a good grip on the printer. Handles are automatically added if you select enclosure.



#### LED LIGHTS
- Frame LEDs - RECOMMENDED - LED strips mounted on the frame in the nozzle height to better see the prints.
- Enclosure LEDs - RECOMMENDED - LED strips mounted on the upper edge of the enclosure to light up the inside of the printer.



#### AUX COOLING
Auxiliary side cooling using 12032 fans blowing air over the build plate from both sides. For more powerful cooling for your prints.



#### BED WIRING - WAGO 221
For running bed heater cables from your board into the connectors mounted on the bed carriage. It helps with serviceability as you can remove the bed completely without removing all the cables. It uses Wago 221 connectors for the heater wiring and JST XH connectors for the thermistor and/or under bed fan.
- DC BED - for DC - usually 24V bed heaters.
- AC BED - for AC bed heaters including connector for the ground wire.



#### UNDER BED FAN
RECOMMENDED if you install enclosure. Helps circulating the air inside the chamber and heating it faster and more evenly by sucking the warm air from below the heated bed and blowing it down. It also helps moving/mixing air in the entire enclosure making it more evenly heated.



#### AUTO Z - VORON
Original Voron design for Auto-Z offset with using "Sexbolt" nozzle endstop.



continue to:
{: .text-right .lh-0 .pt-8 }

[SOURCING PARTS]{: .btn .fs-6 .fw-300 .text-yellow-300 }
{: .text-right }

[CONFIGURATOR DOWNLOAD]: ./assets/docs/E3NG_BOM_241025.xlsm
[BASE BUILD]: https://rh3d.xyz/configure.html#base-build
[TOOLHEAD]: https://rh3d.xyz/configure.html#toolhead
[MODS / UPGRADES]: https://rh3d.xyz/configure.html#mods--upgrades
[SOURCING PARTS]: https://rh3d.xyz/sourcing.html

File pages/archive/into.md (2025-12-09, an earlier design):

---
#title: Into the project
layout: default
has_children: true
nav_order: 30
permalink: /into.html
---
# INTO THE PROJECT
{: .text-center }
Below you will find all the important links to get the files and details needed for the project.

[Printables]{: .btn .fw-400 .text-yellow-300 .v-align-middle .px-7 } - Download STL files and see the changelog.

[Ko-Fi]{: .btn .fw-400 .text-yellow-300 .v-align-middle .px-9 } - Download CAD files for a small amount.

[Calibration cube]{: .btn .fw-400 .text-yellow-300 .v-align-middle .pr-4 .pl-4 } - Download E3NG calibration cube.

[Configurator]{: .btn .fw-400 .text-yellow-300 .v-align-middle .px-6 } - Bill of material, printed parts list and more.

[Build manual]{: .btn .fw-400 .text-yellow-300 .v-align-middle .px-6 } - Instructions to build the printer.

[Join the Discord]{: .btn .fw-400 .text-yellow-300 .v-align-middle .pr-5 .pl-4 } - Join the community and other builders.

[Support my work]{: .btn .fw-400 .text-yellow-300 .v-align-middle } - Directly support the project / creator.

[Instagram]{: .btn .fw-400 .text-yellow-300 .v-align-middle } or [YouTube]{: .btn .fw-400 .text-yellow-300 .v-align-middle } - Graphic content about the project.

It is highly recommended to first start with the stock project so you will follow the clear path, get complete and right instructions and lists and then start modifying with user mods if you want to.
Most remixes / mods are posted on [Printables remixes] but you will also find other on the Discord server. There are also many [remixes for the beta] version and majority of them will still be compatible.

# PROJECT OPTIONS
{: .text-center }
Going deeper into the project, you will find that not all the printers are build the same, that is because the project is offering various options to configure it to your liking right from the start.

Ender 3 NG started as a cheap coreXY conversion for Creality Ender 3 Pro, it has been in the beta version and available to public for over a year and while others have been building printers, I have been listening to all the feedback and getting to know other users preferences.

As a result the project has many options to choose from to suit your needs the best.

continue to:
{: .text-right .lh-0 .pt-8 }

[PRINTER CONFIGURATION]{: .btn .fs-6 .fw-300 .text-yellow-300 }
{: .text-right }

[Printables]: https://www.printables.com/en/model/922401
[Ko-Fi]: https://ko-fi.com/s/f1be48e43a
[Calibration cube]: https://www.printables.com/en/model/478403
[Configurator]: https://rh3d.xyz/E3NG_v1_2/advanced/config
[Build manual]: https://rh3d.xyz/E3NG_v1_2/standard/build_guide
[Join the Discord]: https://discord.com/invite/Zkvu6uu2AR
[Instagram]: https://www.instagram.com/RH3D_cz
[YouTube]: https://www.youtube.com/@RH3D_cz?sub_confirmation=1
[Support my work]: https://rh3d.xyz/donate.html
[Printables remixes]: https://www.printables.com/en/model/922401/remixes
[remixes for the beta]: https://www.printables.com/en/model/469280/remixes
[Printer configuration]: https://rh3d.xyz/E3NG_v1_2/advanced/config

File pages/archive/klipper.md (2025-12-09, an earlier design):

---
title: Klipper FW
layout: default
parent: Printer electronics
#has_children: true
#nav_order: 1
permalink: /klipper.html
---
# KLIPPER FW
{: .text-center }

{: .warning }
This page is under construction.

Officialy supported motherboards:
- [BTT Octopus v1.0]
- [BTT SKR 3 EZ]
- [BTT SKR 3 EZ + BTT EXP-MOT]
- [BTT SKR mini E3 V2]

# BigTreeTech Octopus v1.1
{: .text-center }
[download config files](../assets/fw/blank) | [official BTT documentation](https://github.com/bigtreetech/BIGTREETECH-OCTOPUS-V1.0/tree/master/Hardware) | [buy](https://www.shareasale.com/m-pr.cfm?merchantID=118144&userID=4298933&productID=1380818456)
{: .text-center }
WIRING DIAGRAM HERE
{: .text-center .fs-8 }

# BigTreeTech SKR 3 EZ
{: .text-center }
[download config files](../assets/fw/blank) | [official BTT documentation](https://github.com/bigtreetech/SKR-3/tree/master/Hardware%20(SKR%203%20EZ)) | [buy](https://www.shareasale.com/m-pr.cfm?merchantID=118144&userID=4298933&productID=1380728514)
{: .text-center }
WIRING DIAGRAM HERE
{: .text-center .fs-8 }

# BigTreeTech SKR 3 EZ + BigTreeTech EXP-MOT
{: .text-center }
[download config files](../assets/fw/blank) | [official BTT documentation - SKR3 EZ](https://github.com/bigtreetech/SKR-3/tree/master/Hardware%20(SKR%203%20EZ)) - [EXP-MOT](https://github.com/bigtreetech/BTT-Expansion-module/tree/master/BTT%20EXP-MOT) | [buy SKR 3 EZ](https://www.shareasale.com/m-pr.cfm?merchantID=118144&userID=4298933&productID=1380728514) | [buy EXP-MOT](https://www.shareasale.com/m-pr.cfm?merchantID=118144&userID=4298933&productID=1228986907)
{: .text-center }
WIRING DIAGRAM HERE
{: .text-center .fs-8 }

# BigTreeTech SKR mini E3 V2
{: .text-center }
[download config files](../assets/fw/blank) | [official BTT documentation](https://github.com/bigtreetech/BIGTREETECH-SKR-mini-E3/tree/master/hardware/BTT%20SKR%20MINI%20E3%20V2.0/Hardware) | [buy](https://www.shareasale.com/m-pr.cfm?merchantID=118144&userID=4298933&productID=1228986887)
{: .text-center }
WIRING DIAGRAM HERE
{: .text-center .fs-8 }

[BTT Octopus v1.0]: https://rh3d.xyz/klipper.html#bigtreetech-octopus-v10
[BTT SKR 3 EZ]: https://rh3d.xyz/klipper.html#bigtreetech-skr-3-ez
[BTT SKR 3 EZ + BTT EXP-MOT]: https://rh3d.xyz/klipper.html#bigtreetech-skr-3-ez--bigtreetech-exp-mot
[BTT SKR mini E3 V2]: https://rh3d.xyz/klipper.html#bigtreetech-skr-mini-e3-v2

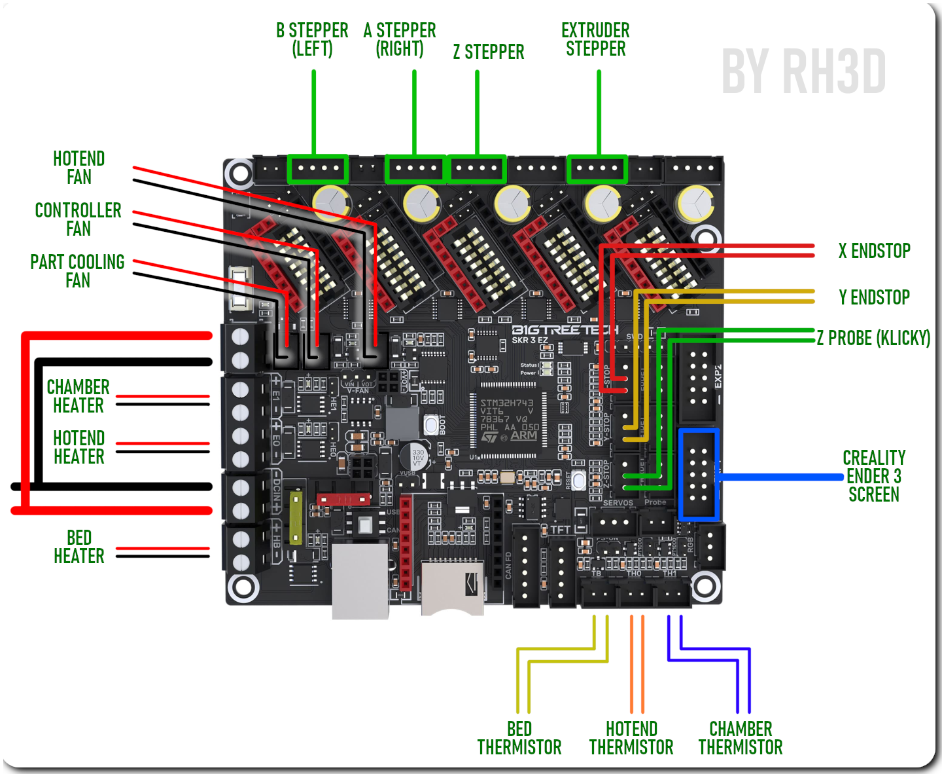
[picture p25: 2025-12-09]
images/diagram/SKR3EZ_MARLIN_WD.png

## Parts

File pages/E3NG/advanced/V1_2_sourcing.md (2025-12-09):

---
title: Sourcing parts
layout: default
parent: v1.2 - (advanced)
grand_parent: E3NG v1.2
has_children: false
nav_order: 20
description: "Source parts for your advanced E3NG v1.2 CoreXY build using the official BOM and configurator. Discover tested links, reuse tips, and advice for modular configurations."
permalink: /E3NG_v1_2/advanced/sourcing_parts
---
# SOURCING PARTS
{: .text-center }

While the **"S"** version was designed to simplify the process by offering a prepared set of parts, this is not possible with the Advanced version. Although the printer base might be similar, each configuration will result in a slightly different final Bill of Materials. The best way to source the parts is to do it manually.

To help with sourcing, you can still check out the available **[KITS]** for the **"S"** version which include some partial packages that may cover most of what you need, offering the advantages of kit pricing and quality. You could even start with a full kit and customize it to suit your requirements.

You'll find all the necessary parts listed in the [configurator's] Bill of Materials. Be sure to pay attention to product quantities, and read the notes and specifications carefully—including required parameters such as dimensions, quality etc.

All linked products have been selected based on our testing, seller reliability, and pricing. That means if you use the recommended links, you'll get parts with a good price-to-performance ratio—where critical components prioritize quality, and others focus on affordability.

continue to:
{: .text-right .lh-0 .pt-8 }

[PRINTING PARTS]{: .btn .fs-6 .fw-300 .text-yellow-300 }
{: .text-right }

[KITS]: https://rh3d.xyz/E3NG_v1_2/standard/sourcing_parts/kits
[configurator's]: https://rh3d.xyz/E3NG_v1_2/advanced/config
[PRINTING PARTS]: https://rh3d.xyz/E3NG_v1_2/advanced/printing_parts

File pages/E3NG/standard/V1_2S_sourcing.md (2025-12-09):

---
title: Sourcing parts
layout: default
parent: v1.2S - (standard)
grand_parent: E3NG v1.2
has_children: true
nav_order: 10
description: "Source parts for your E3NG v1.2S CoreXY build with ease. Choose curated kits for a faster start or follow the full BOM to build your Ender 3 upgrade your way."
permalink: /E3NG_v1_2/standard/sourcing_parts
---
# SOURCING PARTS
{: .text-center }

The "S" version was designed to let users build the printer with minimal extra effort. To support that goal, we prioritized offering kits to eliminate the hassle of sourcing individual parts.

Starting your build with an available kit is the preferred option, as it saves time, reduces complexity, and typically offers a better price-to-performance ratio.

That said, sourcing the parts yourself is still a fully supported alternative.

[KITS]{: .btn .fs-7 .fw-300 .mt-8 .mb-8 .text-yellow-300 .mr-7 }
[BILL OF MATERIAL]{: .btn .fs-7 .fw-300 .mt-8 .mb-8 .text-yellow-300 }
{: .text-center }

[KITS]: https://rh3d.xyz/E3NG_v1_2/standard/sourcing_parts/kits
[BILL OF MATERIAL]: https://rh3d.xyz/E3NG_v1_2/standard/sourcing_parts/self_sourcing

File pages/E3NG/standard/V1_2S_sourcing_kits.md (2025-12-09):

---
title: Kits
layout: default
parent: Sourcing parts
grand_parent: v1.2S - (standard)
has_children: false
nav_order: 10
description: "Explore vendor-supported kits for E3NG v1.2S CoreXY builds. Choose tested components for faster assembly, price-to-performance value, and long-lasting reliability."
permalink: /E3NG_v1_2/standard/sourcing_parts/kits
---

{% include popup.html %}

# KITS
{: .no_toc .text-center }

Only some vendors are officially selling kits - these were assembled in cooperation with us to ensure the parts meet the required quality standards and have been tested for long-lasting performance and great price-to-performance ratio.

However, **we are not the vendor** and are not directly responsible for the service or products offered. If you encounter any issues, please contact the vendor first. Before purchasing, make sure you fully understand what is included in the package.

{: .warning }
Remember that the kits cover all the required parts needed for the conversion but depending on your preferred setup, you might need aditional parts like hotend, extruder, probe etc.

---
*To view the available kits, click the vendor logo:*

<!-- FABREEKO -->
<a href="#" onclick="showPopup('popup1'); return false;">
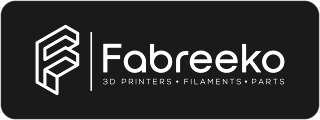
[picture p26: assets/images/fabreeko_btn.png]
  
</a>
{: .text-center }

<div id="popup1" class="popup">
  <span class="close" onclick="hidePopup('popup1')">&times;</span>
  <h1>FABREEKO</h1><br>
  <div style="font-size: 20px; line-height: 1.8;">
    <span style="margin-right: 12px;">🧰</span>
    <a href="https://www.fabreeko.com/products/ender-3-ng-core-xy-conversion-kit-by-honeybadger">E3NG v1.2S full kit</a><br>
    <span style="margin-right: 12px;">📦</span>
    <a href="https://www.fabreeko.com/products/cast-acrylic-panel-set-for-ender-3-ng">ENCLOSURE PANELS - cast acrylic</a><br>
  </div>
    <hr style="margin-top: 30px; border: none; border-top: 1px solid #555;">
  <h3>UPGRADE PARTS</h3><br>
  <div style="font-size: 16px; line-height: 1.6;">
    <span style="margin-right: 12px;">➕</span>
    <a href="https://www.fabreeko.com/products/ender-3-ng-cast-aluminum-bed-by-honeybadger">CNC bed - cast aluminum</a><br>
    <span style="margin-right: 12px;">➕</span>
    <a href="https://www.fabreeko.com/products/ender-3-ng-bed-carriage-by-honeybadger">CNC bed carriage</a><br>
    <span style="margin-right: 12px;">➕</span>
    <a href="https://www.fabreeko.com/products/lmh12uu-bearing-by-honeybadger">LMH12UU for CNC carriage</a>
  </div>
</div>

<!-- FYSETC -->
<a href="#" onclick="showPopup('popup2'); return false;">
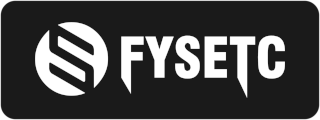
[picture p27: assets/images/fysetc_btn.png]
  
</a>
{: .text-center }

<div id="popup2" class="popup">
  <span class="close" onclick="hidePopup('popup2')">&times;</span>
  <h1>FYSETC</h1><br>
  <div style="font-size: 20px; line-height: 1.8;">
    <span style="margin-right: 12px;">🧰</span>
    <a href="https://s.click.aliexpress.com/e/_oFhekto">E3NG v1.2S full kit (incl. enclosure)</a>
  </div>
  <h3>FYSETC - store</h3><br>
  <div style="font-size: 16px; line-height: 1.6;">
    <span style="margin-right: 12px;">🧰</span>
    <a href="https://www.fysetc.com/products/fysetc-upgraded-kit-for-creality-ender-3-high-quality-3d-printer-parts-corexy-kit-for-ender-3-3d-printers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">E3NG v1.2S full kit (incl. enclosure)</a><br>
   </div>
</div>

<!-- FUNSSOR -->
<a href="#" onclick="showPopup('popup3'); return false;">
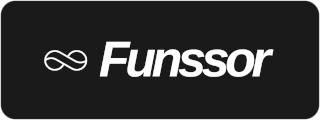
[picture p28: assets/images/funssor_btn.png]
  
</a>
{: .text-center }

<div id="popup3" class="popup">
  <span class="close" onclick="hidePopup('popup3')">&times;</span>
  <h1>FUNSSOR</h1><br>
  <div style="font-size: 20px; line-height: 1.8;">
    <span style="margin-right: 12px;">🧰</span>
    <a href="https://s.click.aliexpress.com/e/_ooF6WBw">E3NG v1.2S kit (no hardware)</a><br>
    <span style="margin-right: 17px;">🔩</span>
    <a href="https://s.click.aliexpress.com/e/_omNZg0k">Hardware</a><br>
    <span style="margin-right: 12px;">📦</span>
    <a href="https://s.click.aliexpress.com/e/_oD5DAoU">ENCLOSURE KIT - polycarbonate</a><br>
  </div>
  <hr style="margin-top: 30px; border: none; border-top: 1px solid #555;">
  <h3>FUNSSORLAB - incl. USA warehouse</h3><br>
  <div style="font-size: 16px; line-height: 1.6;">
    <span style="margin-right: 12px;">🧰</span>
    <a href="https://www.funssorlab.com/products/funssor-ender-3-ng-v12-corexy-conversion-motion-and-electronics-diy-kit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">E3NG v1.2S kit (without hardware)</a><br>
    <span style="margin-right: 16px;">🔩</span>
    <a href="https://www.funssorlab.com/products/funssor-ender-3-ng-v12-corexy-conversion-hardware-screw-nuts-kit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">Hardware</a><br>
    <span style="margin-right: 12px;">📦</span>
    <a href="https://www.funssorlab.com/products/funssor-ender-3-ng-v12-convertion-corexy-3d-printer-upgrade-enclosure-pc-kit-with-screw-pack-optional-4mm-thickness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">ENCLOSURE KIT - polycarbonate</a><br>
  </div>
  <h3>UPGRADE PARTS</h3><br>
  <div style="font-size: 16px; line-height: 1.6;">
    <span style="margin-right: 12px;">➕</span>
    <a href="https://s.click.aliexpress.com/e/_op0VN9i">6MM CNC aluminum bed</a><br>
    <span style="margin-right: 12px;">➕</span>
    <a href="https://s.click.aliexpress.com/e/_oCJYEE0">CNC aluminum bed carriage</a>
  </div>
</div>

<!-- FUSHI -->
<a href="#" onclick="showPopup('popup4'); return false;">
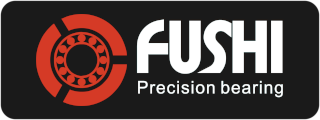
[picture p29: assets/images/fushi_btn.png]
  
</a>
{: .text-center }

<div id="popup4" class="popup">
  <span class="close" onclick="hidePopup('popup4')">&times;</span>
  <h1>FUSHI bearings</h1><br>
  <div style="font-size: 20px; line-height: 1.8;">
    <span style="margin-right: 12px;">⚙️</span>
    <a href="https://s.click.aliexpress.com/e/_oCrZCk4">Bearings and shafts kit</a>
  </div>
</div>

continue to:
{: .text-right .lh-0 .pt-8 }

[PRINTING PARTS]{: .btn .fs-6 .fw-300 .text-yellow-300 }
{: .text-right }

[PRINTING PARTS]: https://rh3d.xyz/E3NG_v1_2/standard/printing_parts

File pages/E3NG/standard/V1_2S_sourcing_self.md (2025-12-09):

---
title: Self sourcing
layout: default
parent: Sourcing parts
grand_parent: v1.2S - (standard)
has_children: false
nav_order: 20
description: "Self-source all parts for your E3NG v1.2S CoreXY build with a detailed BOM, tested links, and reuse tips. Customize your Ender 3 upgrade your way."
permalink: /E3NG_v1_2/standard/sourcing_parts/self_sourcing
---
# SELF SOURCING
{: .text-center }

If you are not interested in buying the complete kit, feel free to source all the parts by yourself and possibly even reuse some other parts laying around.

The links in the Bill of material are for products that have been tested and are of required quality for succesfull build.

{: .warning }
Remember that the BOM covers all the required parts needed for the conversion but depending on your preferred setup, you might need aditional parts like hotend, extruder, probe etc.

*Some of the AliExpress links are affiliate links. They come at no additional cost to you but provide a small commission to us, which helps keep the project and related development alive. Vendor selection was in no way influenced by affiliate availability—quality, price, and seller reliability were our top priorities.*

# BILL OF MATERIAL

## PRINTER HARDWARE
#### SCREWS

| Size | Type/specifications |  Quantity |  Link  |
|:---|:---|:---:|:---:|
| **M2** x 10 | **socket** head `DIN 912 / ISO 4762` | 4 |  [NINDEJIN](https://s.click.aliexpress.com/e/_oEqVeJK)  |
| **M3** x 6  | **socket** head `DIN 912 / ISO 4762` | 72 |  [NINDEJIN](https://s.click.aliexpress.com/e/_oEqVeJK)  |
| **M3** x 8  | **socket** head `DIN 912 / ISO 4762` | 50 |  [NINDEJIN](https://s.click.aliexpress.com/e/_oEqVeJK)  |
| **M3** x 10 | **socket** head `DIN 912 / ISO 4762` | 34 |  [NINDEJIN](https://s.click.aliexpress.com/e/_oEqVeJK)  |
| **M3** x 16 | **socket** head `DIN 912 / ISO 4762` | 4 |  [NINDEJIN](https://s.click.aliexpress.com/e/_oEqVeJK)  |
| **M3** x 20 | **socket** head `DIN 912 / ISO 4762` | 15 |  [NINDEJIN](https://s.click.aliexpress.com/e/_oEqVeJK)  |
| **M3** x 25 | **socket** head `DIN 912 / ISO 4762` | 8 |  [NINDEJIN](https://s.click.aliexpress.com/e/_oEqVeJK)  |
| **M3** x 35 | **socket** head `DIN 912 / ISO 4762` | 11 |  [NINDEJIN](https://s.click.aliexpress.com/e/_oEqVeJK)  |
| **M4** x 8  | **socket** head `DIN 912 / ISO 4762` | 34 |  [NINDEJIN](https://s.click.aliexpress.com/e/_oEqVeJK)  |
| **M4** x 10 | **socket** head `DIN 912 / ISO 4762` | 12 |  [NINDEJIN](https://s.click.aliexpress.com/e/_oEqVeJK)  |
| **M5** x 12 | **socket** head `DIN 912 / ISO 4762` | 24 |  [NINDEJIN](https://s.click.aliexpress.com/e/_oEqVeJK)  |
| **M5** x 20 | **socket** head `DIN 912 / ISO 4762` | 4 |  [NINDEJIN](https://s.click.aliexpress.com/e/_oEqVeJK)  |
| **M5** x 25 | **socket** head `DIN 912 / ISO 4762` | 10 |  [NINDEJIN](https://s.click.aliexpress.com/e/_oEqVeJK)  |
| **M5** x 35 | **socket** head `DIN 912 / ISO 4762` | 4 |  [NINDEJIN](https://s.click.aliexpress.com/e/_oEqVeJK)  |
| **M5** x 10 | **button** head `DIN 938 / ISO 7380` | 4 |  [NINDEJIN](https://s.click.aliexpress.com/e/_oD0jZMY)  |
| **M5** x 20 | **button** head `DIN 938 / ISO 7380` | 20 |  [NINDEJIN](https://s.click.aliexpress.com/e/_oD0jZMY)  |
| **M5** x 30 | **button** head `DIN 938 / ISO 7380` | 4 |  [NINDEJIN](https://s.click.aliexpress.com/e/_oD0jZMY)  |
| **M3** x 5  | **flatpoint** setscrew `DIN 913 / ISO 4026` | 8 |  [NINDEJIN](https://s.click.aliexpress.com/e/_ophdoDW)  |
{: class="transparant_table"}

#### WASHERS, NUTS, T-NUTS, HEAT SET INSERTS

| Size | Type/specifications |  Quantity |  Link  |
|:---|:---|:---:|:---:|
| **M5** | **washer** `DIN 125A / ISO 7089` | 65 |  [NINDEJIN](https://s.click.aliexpress.com/e/_olHMc2g)  |
| **M3** | **hex nut** `DIN 934 / ISO 8673` | 5 |  [NINDEJIN](https://s.click.aliexpress.com/e/_oDy3nla)  |
| **M3** | **T-nut** `for 2020 V-Slot extrusion` | 35 |  [NINDEJIN](https://s.click.aliexpress.com/e/_ooSJSAs)  |
| **M4** | **T-nut** `for 2020 V-Slot extrusion` | 32 |  [NINDEJIN](https://s.click.aliexpress.com/e/_ooSJSAs)  |
| **M3** | **heat set threaded insert** `M3 x L 4 x OD 4,5 mm` | 110 |  [EDGAR GARY st.](https://s.click.aliexpress.com/e/_oB9tEk4)  |
| **M5** | **heat set threaded insert** `M5 x L 5 x OD 7 mm` | 24 |  [EDGAR GARY st.](https://s.click.aliexpress.com/e/_oB9tEk4)  |
{: class="transparant_table"}

## MOTION AND FRAME PARTS
#### BEARINGS

| Size | Type/specifications |  Quantity |  Link  |
|:---|:---|:---:|:---:|
| **LM8LUU** | linear motion bearing `ABEC - 5` | 4 |  [FUSHI](https://s.click.aliexpress.com/e/_ol5zLEy)  |
| **LM12UU**  | linear motion bearing `ABEC - 5`  | 3 |  [FUSHI](https://s.click.aliexpress.com/e/_ol5zLEy)  |
| **F695**-2RS  | flanged ball bearing `ABEC - 5` | 32 |  [FUSHI](https://s.click.aliexpress.com/e/_ol5zLEy)  |
| **608**-2RS | ball bearing | 6 |  [FUSHI](https://s.click.aliexpress.com/e/_ol5zLEy)  |
{: class="transparant_table"}

#### LINEAR RODS

| Size | Type/specifications |  Quantity |  Link  |
|:---|:---|:---:|:---:|
| **8 x 350** mm | linear rod `h6, hardened steel` | 4 |  [FUSHI](https://s.click.aliexpress.com/e/_ol5zLEy)  |
| **12 x 350** mm  | linear rod `h6, hardened steel` | 2 |  [FUSHI](https://s.click.aliexpress.com/e/_ol5zLEy)  |
| **12 x 320** mm  | linear rod `h6, hardened steel` | 1 |  [FUSHI](https://s.click.aliexpress.com/e/_ol5zLEy)  |
{: class="transparant_table"}

#### OTHER - MOTION

| Type | Specifications |  Quantity |  Link  |
|:---|:---|:---:|:---:|
| **GT2** belt | **6 mm x 1140 mm** - closed loop | 1 |  [POWGE](https://s.click.aliexpress.com/e/_onseDGo)  |
| **GT2** belt | **6 mm** - open end `Powge or Gates` | 3 meters |  [POWGE](https://s.click.aliexpress.com/e/_omPS6LE)  |
| **GT2** pulley  | **40T, 8 mm bore, for 6 mm belt** `17mm total width` | 3 |  [POWGE](https://s.click.aliexpress.com/e/_oFO5eja)  |
| **GT2** pulley  | **20T, 5 mm bore, for 6 mm belt** | 3 |  [POWGE](https://s.click.aliexpress.com/e/_opxx7yo)  |
| **Leadscrew**  | **T8/8 - 300 mm** | 3 |  [KINGROON](https://s.click.aliexpress.com/e/_oBpikUG)  |
| **Leadscrew nut**  | **T8/8 - round shape, 4 holes**  | 3 |  [KINGROON](https://s.click.aliexpress.com/e/_oBpikUG)  |
{: class="transparant_table"}

#### OTHER

| Type | Specifications |  Quantity |  Link  |
|:---|:---|:---:|:---:|
| extrusion | **2040 - 350 mm V-Slot** `black` | 2 |  [VEEKAFT](https://s.click.aliexpress.com/e/_olW0kS0)  |
| extrusion | **2040 - 300 mm V-Slot** `black` | 2 |  [VEEKAFT](https://s.click.aliexpress.com/e/_olW0kS0)  |
| PTFE tube  | **OD 4 x ID 2 mm**  | 1 meter |  [MELLOW 3D](https://s.click.aliexpress.com/e/_ooNy9K4)  |
| Rubber feet  | hole for **M5** screw, OD 27 mm base | 4 |  [AliExpress](https://s.click.aliexpress.com/e/_opKmyGk)  |
| Bed spacer  | silicone spacer, hole for **M4** screw | 4 |  [CREALITY 3D](https://s.click.aliexpress.com/e/_oBIiCGc)  |
{: class="transparant_table"}

## ELECTRONICS
#### FANS

| Type | Specifications |  Quantity |  Link  |
|:---|:---|:---:|:---:|
| **3010** fan | **axial** fan `24V, dual ball bearing, HIGH RPM` | 1 |  [GDStime](https://s.click.aliexpress.com/e/_oCNiPq4)  |
| **4010** fan | **radial** fan `24V, dual ball bearing, HIGH RPM`  | 2 |  [GDStime](https://s.click.aliexpress.com/e/_oEyKaE0)  |
| **6015** fan  | **axial** fan `24V, dual ball bearing` | 2 |  [WINSINN](https://s.click.aliexpress.com/e/_oEQKmNI)  |
{: class="transparant_table"}

#### OTHER

| Type | Specifications |  Quantity |  Link  |
|:---|:---|:---:|:---:|
| DIN rail | **35 x 350** mm | 2 |  [AliExpress](https://s.click.aliexpress.com/e/_ookAI5W)  |
| DIN rail | **35 x 200** mm | 1 |  [AliExpress](https://s.click.aliexpress.com/e/_ookAI5W)  |
| microswitch | `Omron D2F-L` | 3 |  [AliExpress](https://s.click.aliexpress.com/e/_ompcb2M)  |
{: class="transparant_table"}

## ENCLOSURE
#### PANELS
*DXF files are available at printables.*

| Type | Specifications |  Quantity |  Link  |
|:---|:---|:---:|:---:|
| PANEL KIT | **5 mm** door panel, other panels **4 mm** | 1 |  [FUNSSOR](https://s.click.aliexpress.com/e/_oCO1L0o)  |
{: class="transparant_table"}

#### OTHER

| Type | Specifications |  Quantity |  Link  |
|:---|:---|:---:|:---:|
| **F695**-2RS | flanged ball bearing `ABEC - 5` | 12 |  [FUSHI](https://s.click.aliexpress.com/e/_ol5zLEy)  |
| **6015** fan  | **axial** fan `24V, dual ball bearing` | 1 |  [WINSINN](https://s.click.aliexpress.com/e/_oEQKmNI)  |
| **N42** magnet  | **OD 6 x L 3** mm - neodymium magnet | 20 |  ---  |
{: class="transparant_table"}

#### HARDWARE

| Size | Type/specifications |  Quantity |  Link  |
|:---|:---|:---:|:---:|
| **M3** x 6  | **socket** head `DIN 912 / ISO 4762` | 2 |  [NINDEJIN](https://s.click.aliexpress.com/e/_oEqVeJK)  |
| **M3** x 10 | **socket** head `DIN 912 / ISO 4762` | 51 |  [NINDEJIN](https://s.click.aliexpress.com/e/_oEqVeJK)  |
| **M3** x 14 | **socket** head `DIN 912 / ISO 4762` | 17 |  [NINDEJIN](https://s.click.aliexpress.com/e/_oEqVeJK)  |
| **M3** x 25 | **socket** head `DIN 912 / ISO 4762` | 4 |  [NINDEJIN](https://s.click.aliexpress.com/e/_oEqVeJK)  |
| **M3** x 35 | **socket** head `DIN 912 / ISO 4762` | 2 |  [NINDEJIN](https://s.click.aliexpress.com/e/_oEqVeJK)  |
| **M5** x 12 | **socket** head `DIN 912 / ISO 4762` | 12 |  [NINDEJIN](https://s.click.aliexpress.com/e/_oEqVeJK)  |
| **M3** x 12 | **countersunk** head `DIN 7991 / ISO 10642` | 12 |  [NINDEJIN](https://s.click.aliexpress.com/e/_okNhDfW)  |
| **M5** | **washer** `DIN 125A / ISO 7089` | 12 |  [NINDEJIN](https://s.click.aliexpress.com/e/_olHMc2g)  |
| **M3** | **T-nut** `for 2020 V-Slot extrusion` | 46 |  [NINDEJIN](https://s.click.aliexpress.com/e/_ooSJSAs)  |
| **M3** | **heat set threaded insert** `M3 x L 4 x OD 4,5 mm` | 41 |  [EDGAR GARY st.](https://s.click.aliexpress.com/e/_oB9tEk4)  |
| **M5** | **heat set threaded insert** `M5 x L 5 x OD 7 mm` | 12 |  [EDGAR GARY st.](https://s.click.aliexpress.com/e/_oB9tEk4)  |
{: class="transparant_table"}

continue to:
{: .text-right .lh-0 .pt-8 }

[PRINTING PARTS]{: .btn .fs-6 .fw-300 .text-yellow-300 }
{: .text-right }

[PRINTING PARTS]: https://rh3d.xyz/E3NG_v1_2/standard/printing_parts

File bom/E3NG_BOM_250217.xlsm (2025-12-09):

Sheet: BILL OF MATERIAL
 | BACK TO: |  |  |  | GO TO:
NAME |  | PCS | NOTE | MAIN LINK |  | ALT. LINK | PRICE
HARDWARE |  |  | Minimal amount is calculated here – always buy some extra. |  |  |  | $37.75
M2 SCREWS – SOCKET HEAD
 | M2x10 | 4 |  | [ AliExpress ] (https://s.click.aliexpress.com/e/_DBWDdt9) |  |  | $0.09
M2,5 SCREWS – SOCKET HEAD
 | M2,5x6 | 0 | May be included with your hotend. | [ AliExpress ] (https://s.click.aliexpress.com/e/_DBWDdt9) |  |  | $0.00
 | M2,5x8 | 4 | May be included with your hotend. | [ AliExpress ] (https://s.click.aliexpress.com/e/_DBWDdt9) |  |  | $0.09
M3 SCREWS – SOCKET HEAD |  | 0
 | M3x6 | 69 |  | [ AliExpress ] (https://s.click.aliexpress.com/e/_DBWDdt9) |  |  | $1.63
 | M3x8 | 44 |  | [ AliExpress ] (https://s.click.aliexpress.com/e/_DBWDdt9) |  |  | $1.12
 | M3x10 | 32 |  | [ AliExpress ] (https://s.click.aliexpress.com/e/_DBWDdt9) |  |  | $0.87
 | M3x14 | 0 |  | [ AliExpress ] (https://s.click.aliexpress.com/e/_DBWDdt9) |  |  | $0.00
 | M3x16 | 4 |  | [ AliExpress ] (https://s.click.aliexpress.com/e/_DBWDdt9) |  |  | $0.14
 | M3x20 | 15 |  | [ AliExpress ] (https://s.click.aliexpress.com/e/_DBWDdt9) |  |  | $0.62
 | M3x25 | 8 |  | [ AliExpress ] (https://s.click.aliexpress.com/e/_DBWDdt9) |  |  | $0.69
 | M3x30 | 0 |  | [ AliExpress ] (https://s.click.aliexpress.com/e/_DBWDdt9) |  |  | $0.00
 | M3x35 | 11 |  | [ AliExpress ] (https://s.click.aliexpress.com/e/_DBWDdt9) |  |  | $1.08
M3 SCREWS – BUTTON HEAD
 | M3x6 | 0 |  | [ AliExpress ] (https://s.click.aliexpress.com/e/_Dkgw0T9) |  |  | $0.00
 | M3x14 | 0 |  | [ AliExpress ] (https://s.click.aliexpress.com/e/_Dkgw0T9) |  |  | $0.00
 | M3x18 | 0 |  | [ AliExpress ] (https://s.click.aliexpress.com/e/_Dkgw0T9) |  |  | $0.00
M3 SCREWS – FLAT HEAD COUNTERSUNK
 | M3x12 | 0 |  | [ AliExpress ] (https://s.click.aliexpress.com/e/_DkmPmLl) |  |  | $0.00
M4 SCREWS – SOCKET HEAD
 | M4x6 | 0 |  | [ AliExpress ] (https://s.click.aliexpress.com/e/_DBWDdt9) |  |  | $0.00
 | M4x8 | 32 |  | [ AliExpress ] (https://s.click.aliexpress.com/e/_DBWDdt9) |  |  | $3.02
 | M4x10 | 11 |  | [ AliExpress ] (https://s.click.aliexpress.com/e/_DBWDdt9) |  |  | $1.09
M5 SCREWS – SOCKET HEAD
 | M5x12 | 24 |  | [ AliExpress ] (https://s.click.aliexpress.com/e/_DBWDdt9) |  |  | $4.30
 | M5x20 | 4 |  | [ AliExpress ] (https://s.click.aliexpress.com/e/_DBWDdt9) |  |  | $0.99
 | M5x25 | 10 |  | [ AliExpress ] (https://s.click.aliexpress.com/e/_DBWDdt9) |  |  | $2.76
 | M5x35 | 4 |  | [ AliExpress ] (https://s.click.aliexpress.com/e/_DBWDdt9) |  |  | $1.22
M5 SCREWS – BUTTON HEAD
 | M5x10 | 4 |  | [ AliExpress ] (https://s.click.aliexpress.com/e/_Dkgw0T9) |  |  | $0.88
 | M5x20 | 20 |  | [ AliExpress ] (https://s.click.aliexpress.com/e/_Dkgw0T9) |  |  | $5.38
 | M5x30 | 0 |  | [ AliExpress ] (https://s.click.aliexpress.com/e/_Dkgw0T9) |  |  | $0.00
SETSCREWS
 | M3x5 flatpoint | 8 |  | [ AliExpress ] (https://s.click.aliexpress.com/e/_DkiENll) |  |  | $0.18
WASHERS
 | M3 | 0 | 3,2 x 7 x 0,5 mm (ID x OD x TH) - Brass washers have less burr = more precision (alt. link). | [ AliExpress ] (https://s.click.aliexpress.com/e/_DDPuj0x) |  | [ AliExpress ] (https://s.click.aliexpress.com/e/_DEalBbD) | $0.00
 | M5 | 60 | 5,3 x 10 x 1 mm (ID x OD x TH) - Brass washers have less burr = more precision (alt. link). | [ AliExpress ] (https://s.click.aliexpress.com/e/_DDPuj0x) |  | [ AliExpress ] (https://s.click.aliexpress.com/e/_DEalBbD) | $1.08
NUTS
 | M3 | 5 |  | [ AliExpress ] (https://s.click.aliexpress.com/e/_DmT9lb1) |  |  | $0.12
T-NUTS
 | M3 | 31 | Roll-in T-nuts from alternative link are much nicer to work with but are more expensive than hammer T-nuts. | [ AliExpress ] (https://s.click.aliexpress.com/e/_DEGb5AB) |  | [ AliExpress ] (https://s.click.aliexpress.com/e/_DnbMrU7) | $1.96
 | M4 | 30 | Roll-in T-nuts from alternative link are much nicer to work with but are more expensive than hammer T-nuts. | [ AliExpress ] (https://s.click.aliexpress.com/e/_DEGb5AB) |  | [ AliExpress ] (https://s.click.aliexpress.com/e/_DnbMrU7) | $1.80
HEAT INSERTS
 | M3 | 103 | M3 x 4 x 4,5 mm (ID x L x OD) | [ AliExpress ] (https://s.click.aliexpress.com/e/_Dl2dfm3) |  |  | $4.32
 | M5 | 18 | M5 x 5 x 7 mm (ID x L x OD) | [ AliExpress ] (https://s.click.aliexpress.com/e/_Dl2dfm3) |  |  | $1.17
MAGNETS
 | MAGNET 6x3 | 8 |  | [ AliExpress ] (https://s.click.aliexpress.com/e/_DC1MEgn) |  |  | $1.16
MOTION |  |  |  |  |  |  | $147.91
 | 8 x 350 mm linear rod | 4 | h6 diameter tolerance / Ra 0.4 surface roughness / hardened steel = recommended parameters | [ AliExpress ] (https://s.click.aliexpress.com/e/_DkUaS07) |  | [ AliExpress ] (https://s.click.aliexpress.com/e/_DmsqUkb) | $20.02
 | 12 x 350 mm linear rod | 2 | h6 diameter tolerance / Ra 0.4 surface roughness / hardened steel = recommended parameters | [ AliExpress ] (https://s.click.aliexpress.com/e/_DkUaS07) |  | [ AliExpress ] (https://s.click.aliexpress.com/e/_DmsqUkb) | $14.57
 | 12 x 320 mm linear rod | 1 | h6 diameter tolerance / Ra 0.4 surface roughness / hardened steel = recommended parameters | [ AliExpress ] (https://s.click.aliexpress.com/e/_DkUaS07) |  | [ AliExpress ] (https://s.click.aliexpress.com/e/_DmsqUkb) | $7.29
 | LM8LUU linear bearing | 4 | ABEC-5 is recommended minimum | [ AliExpress ] (https://s.click.aliexpress.com/e/_DkUaS07) | [ AliExpress ] (https://s.click.aliexpress.com/e/_DCznNld) | [ AliExpress ] (https://s.click.aliexpress.com/e/_DFlFCB9) | $16.19
 | LM12UU linear bearing | 3 | ABEC-5 is recommended minimum | [ AliExpress ] (https://s.click.aliexpress.com/e/_DkUaS07) |  | [ AliExpress ] (https://s.click.aliexpress.com/e/_DdJb1Or) | $10.88
 | LMH12UU linear bearing | 0 | ABEC-5 is recommended minimum | [ AliExpress ] (https://s.click.aliexpress.com/e/_DmWBVi3) |  |  | $0.00
 | T8/8 x 300 mm leadscrew | 3 |  | [ AliExpress ] (https://s.click.aliexpress.com/e/_DEXYpXh) |  |  | $15.81
 | T8/8 leadscrew nut | 3 |  | included with leadscrew |  |  | $0.00
 | 608-2RS ball bearing | 6 |  | [ AliExpress ] (https://s.click.aliexpress.com/e/_DFyjM75) |  |  | $4.79
 | F695-2RS ball bearing | 32 | There are 28 F695 bearings in the XY motion that need to be better quality, other can theoretically be cheaper. | [ AliExpress ] (https://s.click.aliexpress.com/e/_Dns0msn) |  |  | $17.47
 | 40T 8mm GT2 pulley | 3 | 40T / 8 mm bore / GT2 / for 6 mm belt / total width 17 mm | [ AliExpress ] (https://s.click.aliexpress.com/e/_DnP5ReP) |  |  | $11.99
 | 20T 5mm GT2 pulley | 3 | 20T / 5 mm bore / GT2 / for 6 mm belt | [ AliExpress ] (https://s.click.aliexpress.com/e/_DkTLLPh) |  |  | $4.79
 | 6mm GT2 belt 3m | 1 | 6 mm / 3 m / GT2 / open end – 3 m is minimal, 5 m is recommended – Gates or Powge recommended | [ AliExpress ] (https://s.click.aliexpress.com/e/_DEnxEmX) |  |  | $18.99
 | 6mm GT2 belt 1140 mm closed loop | 1 | 6 mm / 570T / 1140 mm / GT2 / closed loop – recommended length – Gates or Powge recommended | [ AliExpress ] (https://s.click.aliexpress.com/e/_DcAzipl) |  |  | $5.12
 | 6mm GT2 belt 220 mm closed loop | 0 | 6 mm / 110T / 220 mm / GT2 / closed loop – minimal length, longer belt will fit too – Gates or Powge recommended | [ AliExpress ] (https://s.click.aliexpress.com/e/_DFjCNKx) |  |  | $0.00
 | Nema 17 stepper motor | 3 | Stock Creality stepper motors can be used, for the XY motion even with the stock pulleys. | links in the table below |  |  | $0.00
FRAME |  |  |  |  |  |  | $51.75
 | 2040 x 350 mm V-slot extrusion | 2 |  | [ AliExpress ] (https://s.click.aliexpress.com/e/_DmXA93z) |  |  | $14.90
 | 2040 x 300 mm V-slot extrusion | 2 | If you are cutting the extrusions, you can use 2040 x 310 mm extrusions here. | [ AliExpress ] (https://s.click.aliexpress.com/e/_DmXA93z) |  |  | $13.68
 | Rear electronics panel | 1 | Clear or black / polycarbonate or acrylic / recommended thickness 3mm | [ AliExpress ] (https://s.click.aliexpress.com/e/_Dmm2PXP) |  |  | $20.00
 | Enclosure panels - door | 0 | Clear / polycarbonate / recommended thickness 5mm | [ AliExpress ] (https://s.click.aliexpress.com/e/_Dmm2PXP) |  |  | $0.00
 | Enclosure panels - side | 0 | Clear / polycarbonate / recommended thickness 4mm | [ AliExpress ] (https://s.click.aliexpress.com/e/_Dmm2PXP) |  |  | $0.00
 | Enclosure panels - bottom | 0 | Clear or black / polycarbonate / recommended thickness 4mm | [ AliExpress ] (https://s.click.aliexpress.com/e/_Dmm2PXP) |  |  | $0.00
 | Enclosure panels - top | 0 | Clear / polycarbonate / recommended thickness 4mm | [ AliExpress ] (https://s.click.aliexpress.com/e/_Dmm2PXP) |  |  | $0.00
 | Enclosure panels - rear | 0 | Clear or black / polycarbonate / recommended thickness 4mm | [ AliExpress ] (https://s.click.aliexpress.com/e/_Dmm2PXP) |  |  | $0.00
 | RUBBER FEET | 4 |  | [ AliExpress ] (https://s.click.aliexpress.com/e/_DDPQD39) |  |  | $3.17
 | 2020 x 330 mm V-slot extrusion | 1 | stock Ender 3 Pro extrusion - top frame bar |  |  |  | $0.00
 | 2020 x 345 mm V-slot extrusion | 1 | stock Ender 3 Pro extrusion - X axis / M5 tapped end holes required |  |  |  | $0.00
 | 2040 x 400 mm V-slot extrusion | 2 | stock Ender 3 Pro extrusion - frame vertical supports / M5 tapped end holes required |  |  |  | $0.00
 | 4040 x 350 mm V-slot extrusion | 1 | stock Ender 3 Pro extrusion - Y axis / M5 tapped end holes required |  |  |  | $0.00
 | 4040 x 290 mm V-slot extrusion | 2 | stock Ender 3 Pro extrusion - bottom frame sides / M5 tapped end holes required |  |  |  | $0.00
ELECTRONICS |  |  |  |  |  |  | $42.70
 | DIN rail 350 mm | 2 |  | [ AliExpress ] (https://s.click.aliexpress.com/e/_Dkhvg7V) |  |  | $7.16
 | DIN rail 200 mm | 1 |  | [ AliExpress ] (https://s.click.aliexpress.com/e/_Dkhvg7V) |  |  | $2.93
 | 3010 axial FAN | 1 | 24V / dual ball bearing / 12 000 RPM – hotend cooling | [ AliExpress ] (https://s.click.aliexpress.com/e/_Dd633YX) |  |  | $6.12
 | 4010 axial FAN | 0 | 24V – Raspberry Pi cooling | [ AliExpress ] (https://s.click.aliexpress.com/e/_DBbCUYX) |  |  | $0.00
 | 4020 axial FAN | 0 | 24V – AB stepper cooling | [ AliExpress ] (https://s.click.aliexpress.com/e/_DDZ6ED5) | [ Amazon ] (https://amzn.to/4cpsjQv) |  | $0.00
 | 6015 axial FAN | 2 | 24V – electronics cooling + air circulating fan under bed | [ AliExpress ] (https://s.click.aliexpress.com/e/_DBdWLVD) |  |  | $8.01
 | 4010 radial FAN | 2 | 24V / dual ball bearing / 12 000 RPM - part cooling | [ AliExpress ] (https://s.click.aliexpress.com/e/_DlMEeu3) |  |  | $13.78
 | 4020 radial FAN | 0 | 24V / dual ball bearing / 6 500 RPM – part cooling | [ AliExpress ] (https://s.click.aliexpress.com/e/_DCL0wmn) |  |  | $0.00
 | 5015 radial FAN | 0 | 24V / dual ball bearing / 8 500 RPM – part cooling | [ AliExpress ] (https://s.click.aliexpress.com/e/_Ddar97V) | [ Amazon ] (https://amzn.to/3X034js) |  | $0.00
 | 12032 radial FAN | 0 | 24V / 3 000 RPM – auxiliary cooling fan | [ AliExpress ] (https://s.click.aliexpress.com/e/_DDceVoX) | [ Amazon ] (https://amzn.to/4cp63GK) | [ AliExpress ] (https://s.click.aliexpress.com/e/_DlACZQn) | $0.00
 | CPAP | 0 |  | [ AliExpress ] (https://s.click.aliexpress.com/e/_DBHKyvt) | [ Amazon ] (https://amzn.to/3M6Q3hU) | [ AliExpress ] (https://s.click.aliexpress.com/e/_DFhclr1) | $0.00
 | CPAP hose | 0 |  | [ AliExpress ] (https://s.click.aliexpress.com/e/_DBHKyvt) | [ Amazon ] (https://amzn.to/3yH7Hph) | [ AliExpress ] (https://s.click.aliexpress.com/e/_DFExP5N) | $0.00
 | Microswitch | 3 | Omron D2F-L | [ AliExpress ] (https://s.click.aliexpress.com/e/_DcHXdAx) |  |  | $4.09
 | JST 2P FEMALE | 0 |  | [ AliExpress ] (https://s.click.aliexpress.com/e/_DEtWGnv) |  |  | $0.00
 | JST 3P FEMALE | 0 |  | [ AliExpress ] (https://s.click.aliexpress.com/e/_DEtWGnv) |  |  | $0.00
 | WAGO 221-412 | 0 |  | [ AliExpress ] (https://s.click.aliexpress.com/e/_DlnLo6h) |  |  | $0.00
 | PG7 cable gland | 1 | Or use printed version - in the EXTRAS folder | [ AliExpress ] (https://s.click.aliexpress.com/e/_DeiQrCr) |  |  | $0.60
 | LED strips | 0 | 10 mm width / with adhesive / length in meters | [ AliExpress ] (https://s.click.aliexpress.com/e/_DlL7ubp) |  |  | $0.00
 | AC power inlet | 1 | With kill switch and fuse (AC-08) - reuse from your base Ender 3 | [ AliExpress ] (https://s.click.aliexpress.com/e/_DmMINlD) |  |  | $0.00
 | SEXBOLT KIT | 0 | Original Voron style supported | [ AliExpress ] (https://s.click.aliexpress.com/e/_Dejn1Sj) |  |  | $0.00
OTHER HARDWARE |  |  |  |  |  |  | $1.74
 | Bed silicone spacer | 4 |  | [ AliExpress ] (https://s.click.aliexpress.com/e/_DeOq9hH) |  |  | $1.74
 | Bed build plate | 1 |  | [ AliExpress ] (https://s.click.aliexpress.com/e/_DcIz5Nv) |  |  | $0.00
 | WobbleX WS8 | 0 |  | [ AliExpress ] (https://s.click.aliexpress.com/e/_DnoKHUF) |  |  | $0.00
 | PROBE/EXTRUDER KIT | 1 |  | links in the table below |  |  | $0.00
LOOKING FOR SOMETHING ELSE? BOARD, HOTEND, EXTRUDER, PROBE, STEPPERS OR PLANNING UPGRADES?
Section below contains unnecessary parts and components like all of the supported boards, hotends, extruders and probes but also other components that are not specific to the current E3 NG.
If you are buying upgrades, buying it from the list bellow helps supporting the project and doesn’t cost you anything extra. If you choose to do so, thank you very much, you are helping to keep the project alive and growing!
MOTHERBOARDS, SBC
DIRECTLY SUPPORTED BOARDS
 | BTT Octopus v1.1 |  |  | [ AliExpress ] (https://s.click.aliexpress.com/e/_Dd8mCyj) | [ Amazon ] (https://amzn.to/4eDWczd)
 | BTT SKR3EZ |  |  | [ AliExpress ] (https://s.click.aliexpress.com/e/_Dmt9G5z) | [ Amazon ] (https://amzn.to/3KIk8Ue)
 | BTT SKR mini E3 v2 |  |  | [ AliExpress ] (https://s.click.aliexpress.com/e/_DCIOnMr) | [ Amazon ] (https://amzn.to/3KKvmHK)
 | BTT EXP-MOT |  |  | [ AliExpress ] (https://s.click.aliexpress.com/e/_DmSNBDD)
OTHER BOARDS
 | BTT Kraken |  |  | [ AliExpress ] (https://s.click.aliexpress.com/e/_DENgeaR)
 | BTT Manta E3EZ |  |  |  | [ Amazon ] (https://amzn.to/3zfM8Mc)
 | BTT Manta M4P |  |  | [ AliExpress ] (https://s.click.aliexpress.com/e/_Dd3wpST) | [ Amazon ] (https://amzn.to/4c2Lctk)
 | BTT Manta M5P |  |  | [ AliExpress ] (https://s.click.aliexpress.com/e/_Dd3wpST) | [ Amazon ] (https://amzn.to/3VJmBDZ)
 | BTT Manta M8P v1.1 |  |  | [ AliExpress ] (https://s.click.aliexpress.com/e/_DDoMLbV) | [ Amazon ] (https://amzn.to/3xh5eRN)
 | BTT Manta M8P v2.0 |  |  | [ AliExpress ] (https://s.click.aliexpress.com/e/_DFlzjrz) | [ Amazon ] (https://amzn.to/3RzAqm3)
 | BTT Octopus Pro v1.0 |  |  | [ AliExpress ] (https://s.click.aliexpress.com/e/_DFXG9kr) | [ Amazon ] (https://amzn.to/3yXiLOH)
 | BTT Octopus Max EZ v1.0 |  |  | [ AliExpress ] (https://s.click.aliexpress.com/e/_DDza9JN) | [ Amazon ] (https://amzn.to/3RT6lyf)
 | BTT Pico v1.0 |  |  | [ AliExpress ] (https://s.click.aliexpress.com/e/_DkhYdUX) | [ Amazon ] (https://amzn.to/4erisfl)
 | BTT SKR V1.4 / Turbo |  |  | [ AliExpress ] (https://s.click.aliexpress.com/e/_DdcEDLd) | [ Amazon ] (https://amzn.to/3VJcA9Q)
 | BTT SKR 3 |  |  | [ AliExpress ] (https://s.click.aliexpress.com/e/_Dne3a6X) | [ Amazon ] (https://amzn.to/3z5h9m8)
 | BTT SKR mini E3 v3 |  |  | [ AliExpress ] (https://s.click.aliexpress.com/e/_DBHijnH) | [ Amazon ] (https://amzn.to/45pA9If)
 | BTT SKR PRO v1.2 |  |  | [ AliExpress ] (https://s.click.aliexpress.com/e/_DeoVX6T) | [ Amazon ] (https://amzn.to/3VtVwU0)
 | BTT SKRat v1.0 |  |  | [ AliExpress ] (https://s.click.aliexpress.com/e/_Dkat5uB)
SBC
 | BTT CB1 |  |  | [ AliExpress ] (https://s.click.aliexpress.com/e/_De03TYR) | [ Amazon ] (https://amzn.to/4bTEjdL)
 | BTT CB2 |  |  | [ AliExpress ] (https://s.click.aliexpress.com/e/_DE9ieSf)
 | BTT Pi4B |  |  | [ AliExpress ] (https://s.click.aliexpress.com/e/_De03TYR) | [ Amazon ] (https://amzn.to/3z32W9f)
 | BTT Pi v1.2 |  |  | [ AliExpress ] (https://s.click.aliexpress.com/e/_DBVzN5p) | [ Amazon ] (https://amzn.to/3z12etk)
 | BTT Pi v2.0 |  |  | [ AliExpress ] (https://s.click.aliexpress.com/e/_DDh5o7h)
 | Raspberry Pi 4 |  |  |  | [ Amazon ] (https://amzn.to/4csAM5J)
DRIVERS
 | TMC2209 |  |  | [ AliExpress ] (https://s.click.aliexpress.com/e/_DcypCbv) | [ Amazon ] (https://amzn.to/3YInkaq)
 | TMC5160T |  |  | [ AliExpress ] (https://s.click.aliexpress.com/e/_DlbtAjh) | [ Amazon ] (https://amzn.to/4e0OiyL)
 | TMC5160T PRO/PLUS |  |  | [ AliExpress ] (https://s.click.aliexpress.com/e/_DlucEEJ) | [ Amazon ] (https://amzn.to/3yDEZFI)
 | EZ DRIVERS |  |  | [ AliExpress ] (https://s.click.aliexpress.com/e/_De7whGn) | [ Amazon ] (https://amzn.to/3X04udM)
OTHER ELECTRONICS
 | BTT KNOMI v1.0 |  |  | [ AliExpress ] (https://s.click.aliexpress.com/e/_DBAr7nl) | [ Amazon ] (https://amzn.to/45rmobP)
 | BTT KNOMI v2.0 |  |  | [ AliExpress ] (https://s.click.aliexpress.com/e/_DEqop8r) | [ Amazon ] (https://amzn.to/3VLrOLu)
 | BTT PiggyBack36 v1.0 |  |  | [ AliExpress ] (https://s.click.aliexpress.com/e/_DdZhOLv)
 | Mellow Fly-MiniAB board |  |  | [ AliExpress ] (https://s.click.aliexpress.com/e/_DdVCiKP)
 | BTT EBB36 / EBB42 CAN v1.2 |  |  | [ AliExpress ] (https://s.click.aliexpress.com/e/_DePq5LV) | [ Amazon ] (https://amzn.to/45uuTmr)
HOTENDS
DIRECTLY SUPPORTED HOTENDS
 | BambuLab |  |  | [ AliExpress ] (https://s.click.aliexpress.com/e/_DkNYk1V)
 | Creality MK8/CR10 |  |  | [ AliExpress ] (https://s.click.aliexpress.com/e/_DdEE4qn)
 | Creality Spider V3 |  |  |  | [ Amazon ] (https://amzn.to/3VG5MKo)
 | E3D V6 |  |  | [ AliExpress ] (https://s.click.aliexpress.com/e/_DeN3Xaj)
 | E3D V6 Volcano |  |  | [ AliExpress ] (https://s.click.aliexpress.com/e/_Dnmt8C7)
 | E3D Revo Voron |  |  | [ AliExpress ] (https://s.click.aliexpress.com/e/_DnSxmGR)
 | Phaetus Dragonfly BMS |  |  | [ AliExpress ] (https://s.click.aliexpress.com/e/_DEjMiTh) | [ Amazon ] (https://amzn.to/4ewX8oW)
 | Phaetus Dragon 1 SF
 | Phaetus Dragon 1 HF
 | Phaetus Dragon HF
 | Phaetus Rapido HF |  |  | [ AliExpress ] (https://s.click.aliexpress.com/e/_Dmu87A3) | [ Amazon ] (https://amzn.to/3yX0lxv)
 | Phaetus Rapido V2 HF |  |  | [ AliExpress ] (https://s.click.aliexpress.com/e/_DEjq1YJ)
 | Phaetus Dragon UHF |  |  |  | [ Amazon ] (https://amzn.to/3z0K7n9)
 | Phaetus Rapido UHF |  |  | [ AliExpress ] (https://s.click.aliexpress.com/e/_Dmu87A3) | [ Amazon ] (https://amzn.to/3VFVrOn)
 | Phaetus Rapido V2 UHF |  |  | [ AliExpress ] (https://s.click.aliexpress.com/e/_DEjq1YJ)
 | Trianglelab V6DM heatsink |  |  | [ AliExpress ] (https://s.click.aliexpress.com/e/_DnF7Ztt)
 | Triandlelab CHC |  |  | [ AliExpress ] (https://s.click.aliexpress.com/e/_DePwG8F)
 | Trianglelab CHC Pro |  |  | [ AliExpress ] (https://s.click.aliexpress.com/e/_DlJX7x5)
 | Trianglelab TCHC TD6S |  |  | [ AliExpress ] (https://s.click.aliexpress.com/e/_DC8ah6b)
 | Trianglelab CHCB-V TD6S |  |  | [ AliExpress ] (https://s.click.aliexpress.com/e/_Dn424hV)
 | Trianglelab Dragon ACE |  |  | [ trianglelab ] (https://www.trianglelab.net/products/dragon-ace%E2%84%A2-hotend?VariantsId=11348)
 | Trianglelab Dragon ACE+
 | Trianglelab Rapido ACE |  |  | [ AliExpress ] (https://s.click.aliexpress.com/e/_DDGkfkj)
 | VZ - Goliath |  |  | [ AliExpress ] (https://s.click.aliexpress.com/e/_DEZSSSB)
OTHER HOTENDS
ACCESSORIES
 | Meltzone Extender |  |  | [ AliExpress ] (https://s.click.aliexpress.com/e/_DBdKpEx)
 | HT-NTC100K Thermistor |  |  | [ AliExpress ] (https://s.click.aliexpress.com/e/_DdiZTSb)
 | Heater cartridge 24V 50W |  |  | [ AliExpress ] (https://s.click.aliexpress.com/e/_DnoN6UF)
 | Heater cartridge 24V 70W |  |  | [ AliExpress ] (https://s.click.aliexpress.com/e/_DeRvjSj)
FILAMENT EXTRUDERS
 | BMG gear kit - cheap |  | Cheap clone extruder with metal gears, tested. | [ AliExpress ] (https://s.click.aliexpress.com/e/_DmdwzbV)
 | BMG gear kit - cheap |  |  | [ AliExpress ] (https://s.click.aliexpress.com/e/_DBR1sgF)
 | Sherpa gear kit precise |  |  | [ AliExpress ] (https://s.click.aliexpress.com/e/_DF4GICx)
 | Sherpa gear kit precise |  |  | [ AliExpress ] (https://s.click.aliexpress.com/e/_DczrvDt)
 | HGX gear kit |  |  | [ AliExpress ] (https://s.click.aliexpress.com/e/_DEPLVUB)
 | HGX 2.0 gear kit |  |  | [ AliExpress ] (https://s.click.aliexpress.com/e/_Dd4MDeL)
 | Haldis HGX 2.0 extruder |  |  | [ AliExpress ] (https://s.click.aliexpress.com/e/_DmovCZ9)
 | LOD Orbiter v2.0 |  |  | [ AliExpress ] (https://s.click.aliexpress.com/e/_DC9uV75)
 | SLS Sherpa Mini |  |  | [ AliExpress ] (https://s.click.aliexpress.com/e/_DEo9bh1)
 | CNC Vz-Hextrudort |  |  | [ AliExpress ] (https://s.click.aliexpress.com/e/_DlbThIj)
 | CNC Sherpa Micro |  |  | [ AliExpress ] (https://s.click.aliexpress.com/e/_DkfdueB)
 | Voron M4 kit |  |  | [ AliExpress ] (https://s.click.aliexpress.com/e/_DdAPTFH)
BED PROBES
DIRECTLY SUPPORTED PROBES
 | Klicky probe
 | Klicky PCB |  |  | [ AliExpress ] (https://s.click.aliexpress.com/e/_DDbgMTp)
 | BLTouch |  |  | [ AliExpress ] (https://s.click.aliexpress.com/e/_DBdx0j1)
 | CR touch |  |  | [ AliExpress ] (https://s.click.aliexpress.com/e/_DkkNAFt)
 | PINDA |  |  | [ AliExpress ] (https://s.click.aliexpress.com/e/_DFTudCR)
 | Super PINDA |  |  | [ AliExpress ] (https://s.click.aliexpress.com/e/_DmSHN2F)
 | BDSensor |  |  | [ AliExpress ] (https://s.click.aliexpress.com/e/_DmFPMRD) |  | [ AliExpress ] (https://s.click.aliexpress.com/e/_DFLORSn)
 | BDSensor M |  |  | [ AliExpress ] (https://s.click.aliexpress.com/e/_DmFPMRD)
 | Beacon scanner |  |  | [ Beacon3D ] (https://beacon3d.com/product/beacon-h/) | [ AliExpress ] (https://s.click.aliexpress.com/e/_DnoHlQb)
OTHER PROBES
 | BTT EDDY |  |  | [ AliExpress ] (https://s.click.aliexpress.com/e/_Dcjpc6X) | [ Amazon ] (https://amzn.to/45EB33P)
 | BIQU Microprobe |  |  | [ AliExpress ] (https://s.click.aliexpress.com/e/_Dewf3ab)
STEPPER MOTORS
NEMA 17
 | LDO SUPERSLIM |  |  | [ AliExpress ] (https://s.click.aliexpress.com/e/_DdUGjx9)
 | LDO 42STH48 2004MAH |  |  | [ AliExpress ] (https://s.click.aliexpress.com/e/_DFrhMXv)
 | LDO 42STH60 2004AC |  |  | [ AliExpress ] (https://s.click.aliexpress.com/e/_DCv9735)
 | LDO 42STH48 2504AC |  |  | [ AliExpress ] (https://s.click.aliexpress.com/e/_Dl6wkgb)
 | LDO 42STH48 2804AC-R |  |  | [ AliExpress ] (https://s.click.aliexpress.com/e/_DD6Jijv)
 | LDO 42STH48 2804AH-R |  | HIGH TEMP – 180°C | [ AliExpress ] (https://s.click.aliexpress.com/e/_DewDTp1)
 | STEPPERONLINE 42BYGH 17HS19 2004S1 |  |  | [ AliExpress ] (https://s.click.aliexpress.com/e/_DDmR0j1)
 | Wantai 42BYGHW811 |  |  | [ AliExpress ] (https://s.click.aliexpress.com/e/_DdnufmJ)
NEMA 14
 | LDO 36STH17 0354AHG – 8 TEETH |  |  | [ AliExpress ] (https://s.click.aliexpress.com/e/_DkzRUs7)
 | LDO 36STH20 1004AHG – 8 TEETH |  |  | [ AliExpress ] (https://s.click.aliexpress.com/e/_DkzRUs7)
 | LDO 36STH17 0354AHG – 10 TEETH |  |  | [ AliExpress ] (https://s.click.aliexpress.com/e/_Dm976Fv)
 | LDO 36STH20 1004AHG – 10 TEETH |  |  | [ AliExpress ] (https://s.click.aliexpress.com/e/_Dm976Fv)
LOOKING FOR SOME HANDY TOOLS FOR THE BUILD?
Section below contains tools, that are useful for working on 3D printer projects, including the E3NG.
If you buy it from the list bellow, it helps supporting the project and doesn’t cost you anything extra. If you choose to do so, thank you very much, you are helping to keep the project alive and growing!
TOOLS
 | CRIMPING PLIERS |  |  | [ AliExpress ] (https://s.click.aliexpress.com/e/_DCGOuTv)
 | WIRE STRIPPER |  |  | [ AliExpress ] (https://s.click.aliexpress.com/e/_DCdQ4Of)
 | PARALLEL PLIERS |  |  | [ AliExpress ] (https://s.click.aliexpress.com/e/_DFPWuaX)
 | HEX SCREWDRIVERS |  |  | [ AliExpress ] (https://s.click.aliexpress.com/e/_DDiF7cr) |  | [ AliExpress ] (https://s.click.aliexpress.com/e/_DdPoYOn)
 | REAMER |  |  | [ AliExpress ] (https://s.click.aliexpress.com/e/_DCqqHBN)
 | THREAD TAP |  | M4x0,7 + M5x0,8 metric thread | [ AliExpress ] (https://s.click.aliexpress.com/e/_DeYwx3N)
 | FILES |  |  | [ AliExpress ] (https://s.click.aliexpress.com/e/_DkYOKU3)
 | HEAT INSERT TOOL / SOLDERING IRON |  |  | [ AliExpress ] (https://s.click.aliexpress.com/e/_DDKfOY3)
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

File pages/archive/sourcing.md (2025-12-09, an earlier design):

---
title: Sourcing parts
layout: default
parent: Into the project
#has_children: true
nav_order: 2
permalink: /sourcing.html
---
# SOURCING PARTS
{: .text-center }

You have generaly two options to buy your parts - source them yourself with the help of BOM or buy a kit. Both of them have advantages and disadvantages.
{: .text-center }

# SELF SOURCING
{: .text-center }
Is a great way to utilise all your spare parts and save some money but also to absolutely customise the printer to your preferences. With the BOM configurator, you will choose all the options you like and you don't need to buy anything extra. You can also choose where to buy individual products, wait for sales and build or upgrade the printer in stages.

If you decide to selfsource, remember to read the BOM carefully and make sure you understand the needs of specific parts if you are not just following the links.

Bill of material also mentions most of the important parameters for almost every part.

{: .warning }
There are many options to buy your parts with many being significantly cheaper than what is in the BOM. While it is tempting to spend less money, products in the BOM are recommended based on experience of me and many other users. Generally you want reasonable quality for motion system parts - linear shafts, bearings, belts, pulleys etc. You can buy cheaper parts but it is very likely that you will get parts with bad quality and consistency resulting in worse print quality, worse input shaper and overall performance and these will most certainly not last as long as quality products so you will need to spend extra money in time - tested, proven.

# KITS
{: .text-center }
Offering kits for the build is a great way to save your time and to decrease the chance of missing parts because kits have what is needed for the build and are tested by other users.

{: .warning }
No kit is created equal and you have to be carefull as well. With reputable brands like * * * or * * *, you know to be in good hands and you can be sure that these kits are well prepared and have quality parts. But there are also kits that haven't been consulted with me in any way and I would be really carefull here. Some users who bought them often received poorer quality parts or few missing parts which shouldn't happen with verified kits, because low price is not the only priority, it is the balance between cost and quality and for crucial parts, I really insist to have decent quality.

You can find all the verified kits with details and links in the Configurator.

continue to:
{: .text-right .lh-0 .pt-8 }

[PRINTING PARTS]{: .btn .fs-6 .fw-300 .text-yellow-300 }
{: .text-right }

[PRINTING PARTS]: https://rh3d.xyz/printing.html

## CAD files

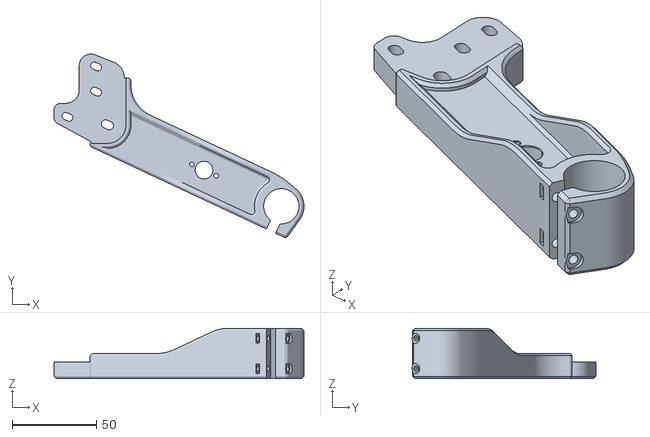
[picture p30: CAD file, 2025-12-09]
models/BED ASSEMBLY/arms/bed_arm_right_solid.stl
148.8 x 109.4 x 30.0

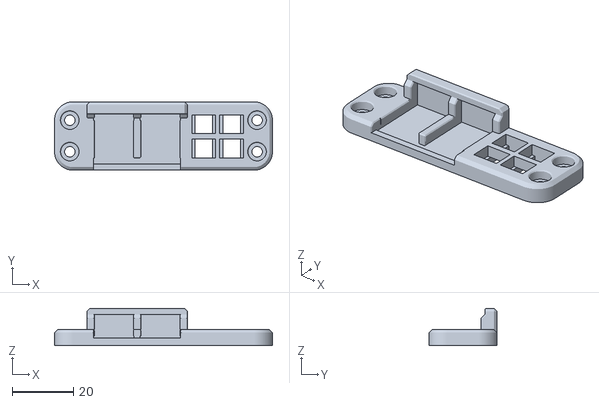
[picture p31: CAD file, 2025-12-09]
models/BED ASSEMBLY/bed_wago221_dc.stl
71.0 x 22.3 x 12.2

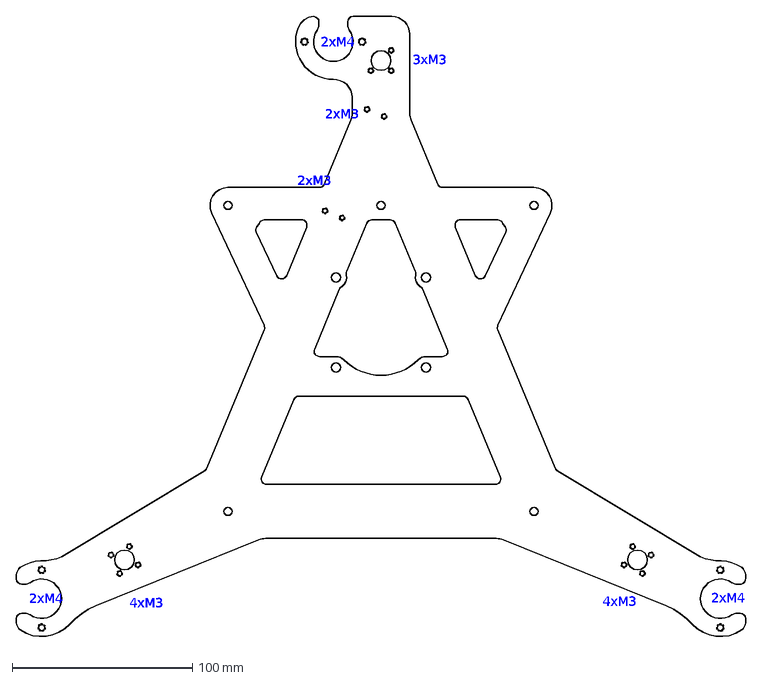
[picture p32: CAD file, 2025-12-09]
models/BED ASSEMBLY/carriage/bed_carriage_metal.dxf
2xM3
2xM4
4xM3
3xM3

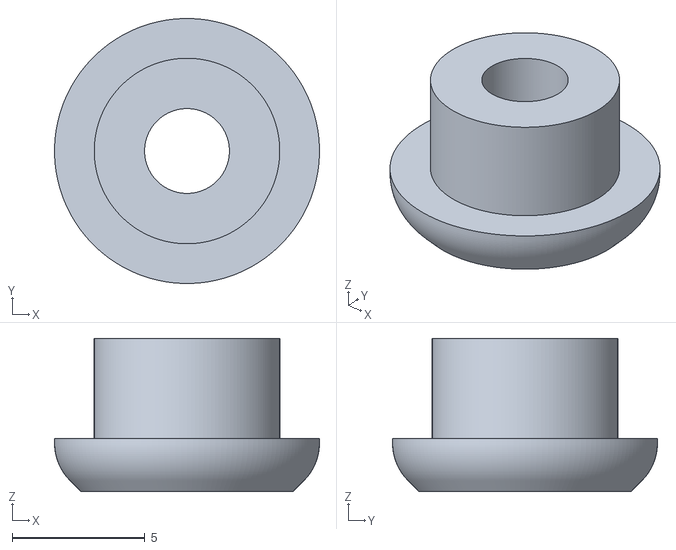
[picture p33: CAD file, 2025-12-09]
models/BED ASSEMBLY/fan/bed_fan_6015_02.stl
10.0 x 10.0 x 5.78

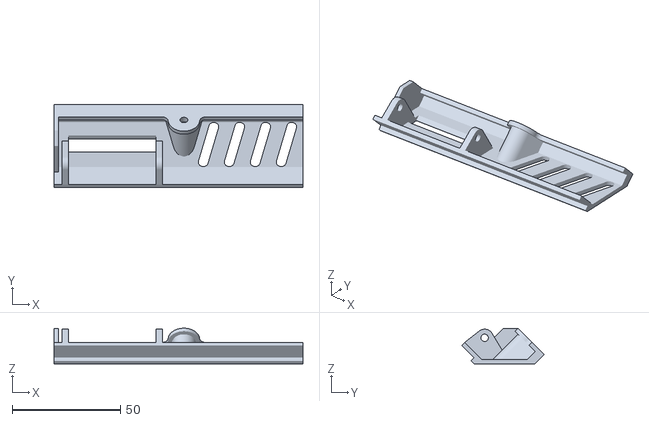
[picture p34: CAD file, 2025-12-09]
models/ENCLOSURE/BACKPACK + ELECTRONICS/electronics_vent_a_upper.stl
115.0 x 38.2 x 16.5

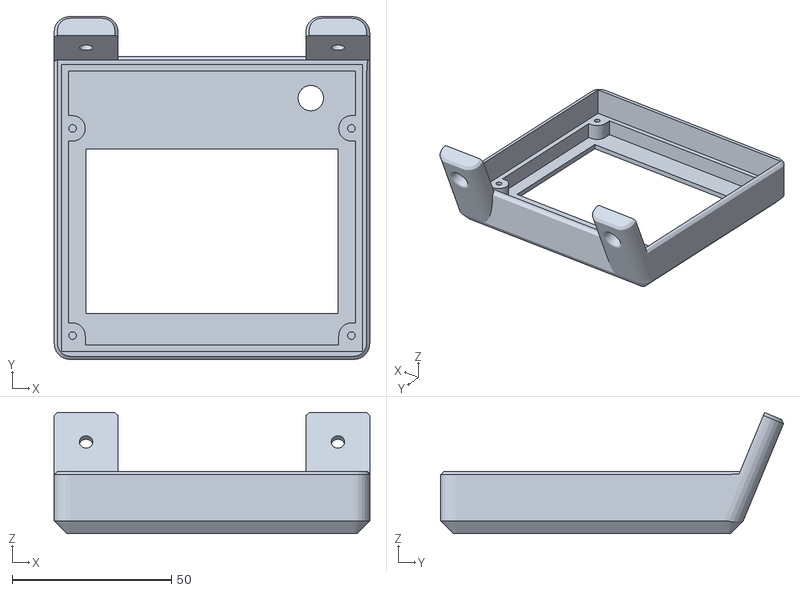
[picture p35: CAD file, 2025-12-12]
models/ENCLOSURE/BACKPACK + ELECTRONICS/ender-3-pro-display-enclosure-for-2020-extrusion-ender-3ng-from-rh3d-model_files/e3pro-display-enclosure-for-2020-extrusion.stl
99.0 x 107.6 x 38.0

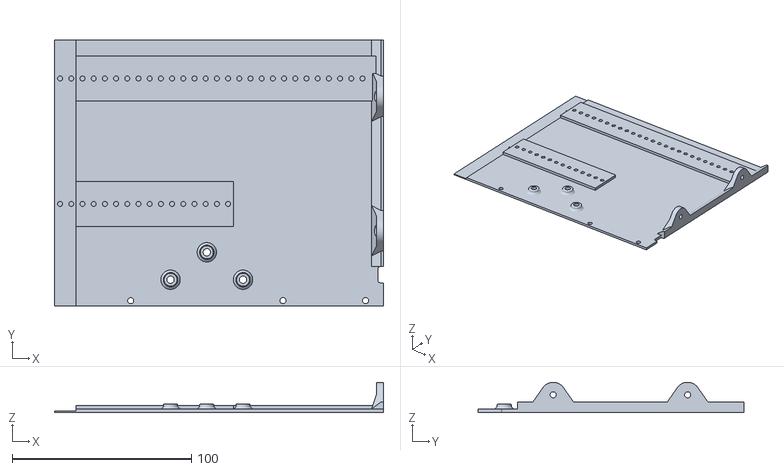
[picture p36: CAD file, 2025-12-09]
models/ENCLOSURE/BACKPACK + ELECTRONICS/panel/electronics_panel_upper_right.stl
183.6 x 148.5 x 17.0

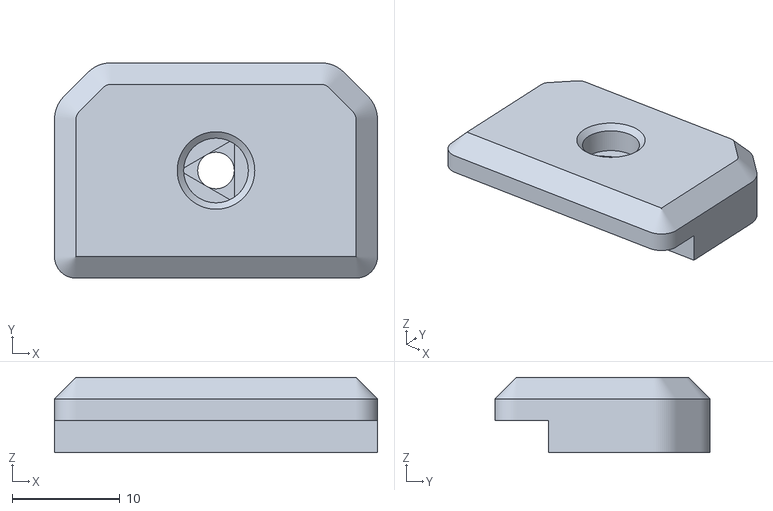
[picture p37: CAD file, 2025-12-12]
models/ENCLOSURE/e3ng-floor-plate-model_files/enclosure_v2_floor_mount.stl
30.0 x 20.0 x 7.00

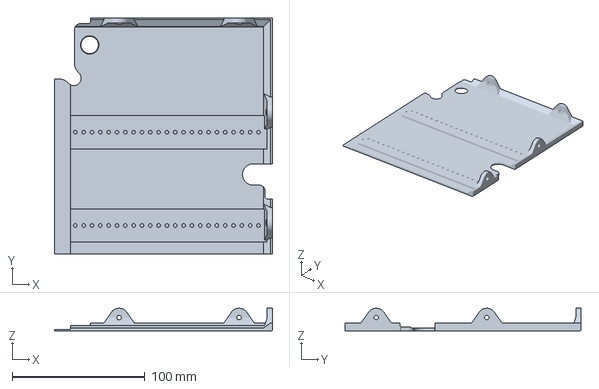
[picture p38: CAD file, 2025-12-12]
models/ENCLOSURE/e3ng-printed-base-plate-model_files/100.2% Scaled Panels/baseplate_panel_back_left_1-motor_scaled.3mf
163.9 x 177.7 x 17.0 mm

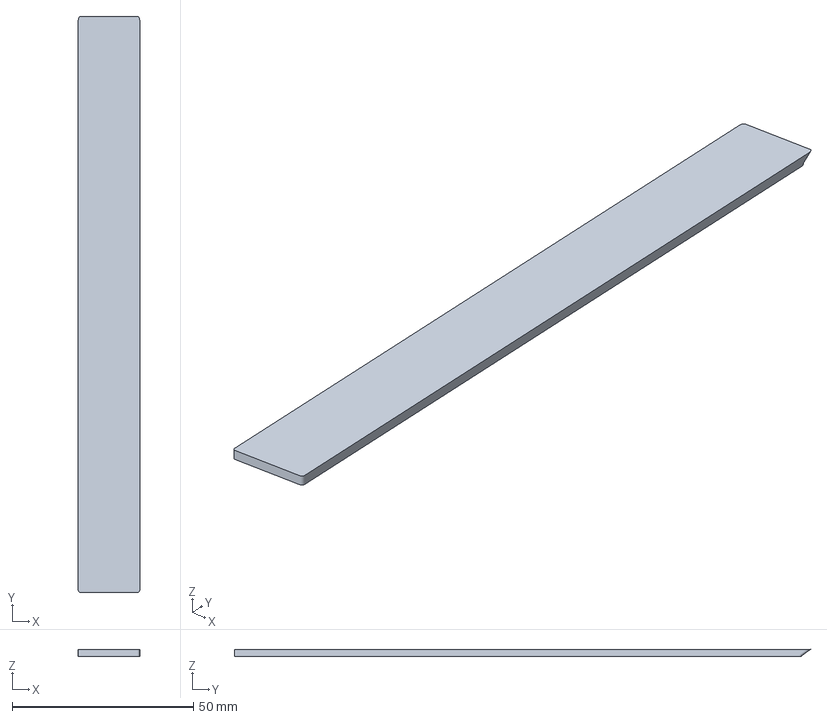
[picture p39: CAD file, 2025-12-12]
models/ENCLOSURE/e3ng-printed-base-plate-model_files/Glue Strips/baseplate_glue_strip_middle-x2.3mf
17.0 x 159.0 x 2.00 mm

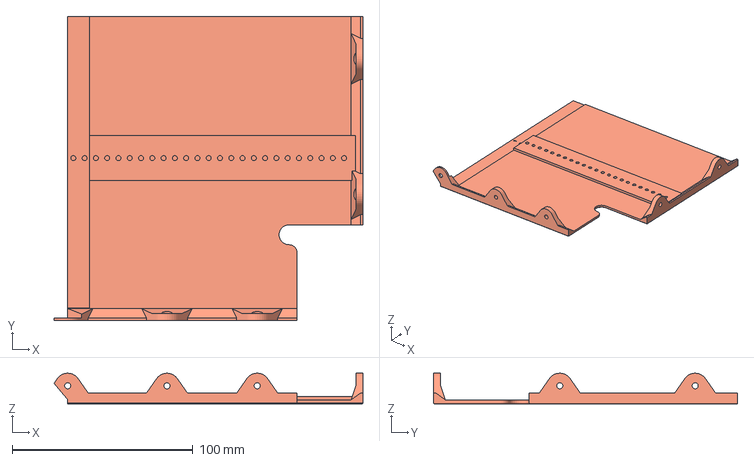
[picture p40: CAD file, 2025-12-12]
models/ENCLOSURE/e3ng-printed-base-plate-model_files/Standard Sized Panels/baseplate_front_left.3mf
171.2 x 168.5 x 17.0 mm

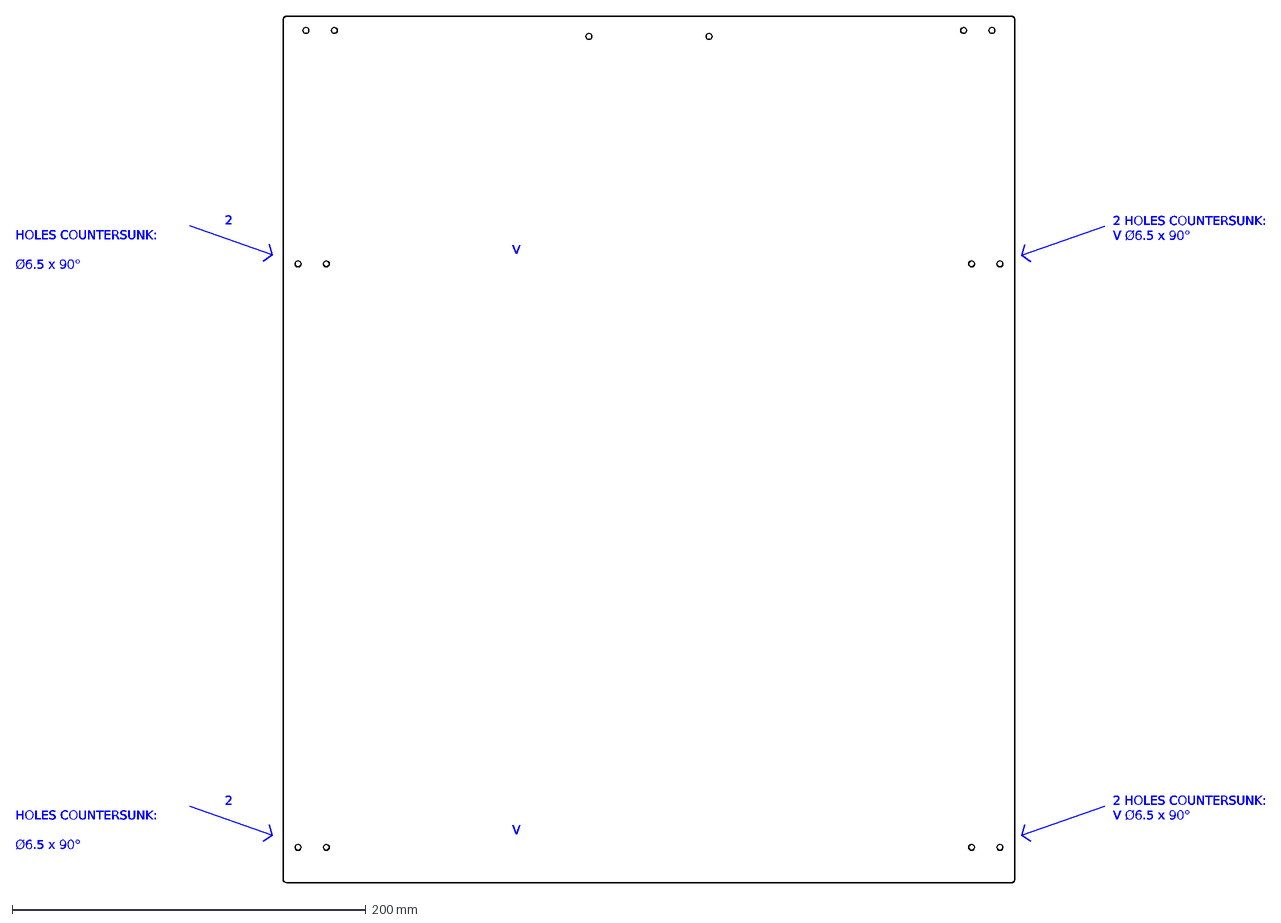
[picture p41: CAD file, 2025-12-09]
models/ENCLOSURE/enclosure_panel_door.dxf
2 HOLES COUNTERSUNK: V Ø6.5 x 90°

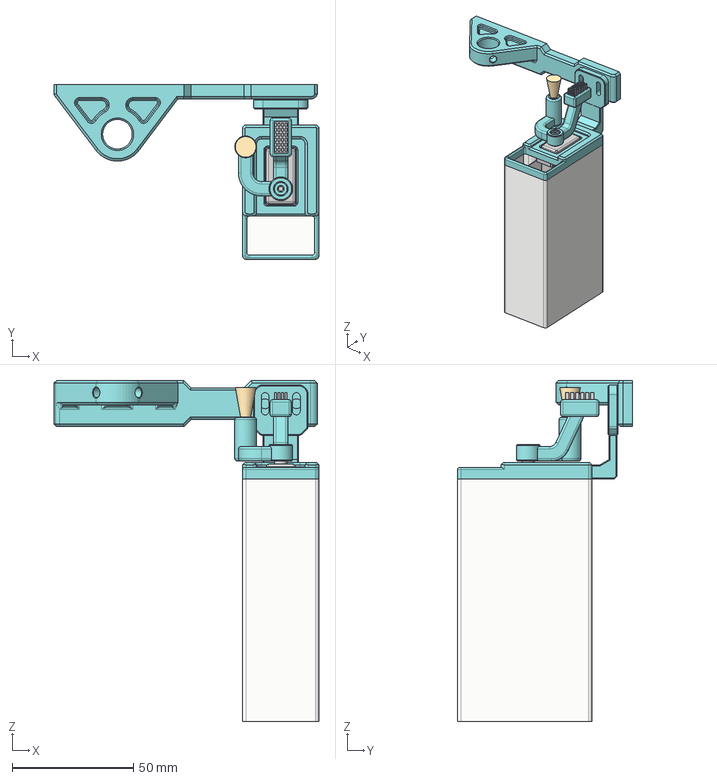
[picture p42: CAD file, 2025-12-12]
models/ENCLOSURE/ender-3-ng-v12-discard-bucket-with-motorized-brass-and-silicone-brushes-model_files/ender-3-ng-v12-discard-bucket-with-motorized-brass-and-silicone-brushes.step
109.3 x 72.1 x 140.6 mm

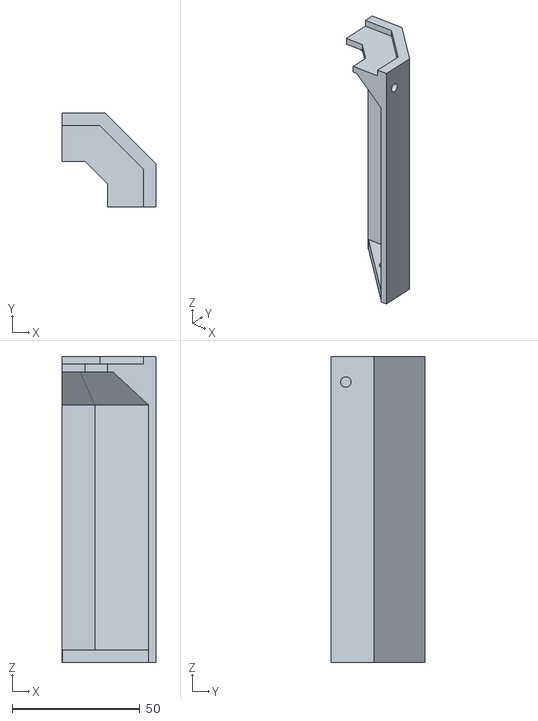
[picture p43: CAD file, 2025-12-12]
models/ENCLOSURE/ender-3-ng-v12-lid-corner-blanks-model_files/ender-3-ng-v12-lid-corner-blanks-right.stl
37.0 x 37.0 x 120.0

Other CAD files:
models/e3ng_logo.dxf
models/ENCLOSURE/ender-3-ng-v12-lid-corners-with-pc4-m6-fittings-model_files/ender-3-ng-v12-lid-corners-with-pc4-m6-fittings.step
models/ENCLOSURE/EXTRAS/electronics_panel_upper_left_dual_color.stl
models/ENCLOSURE/printable-bottom-panel-for-e3ng-v12-model_files/enclosure_panel_bottom_part7.stl
models/BED ASSEMBLY/arms/bed_arm_cover.stl
models/BED ASSEMBLY/arms/bed_arm_insert_flexi_front.stl
models/BED ASSEMBLY/arms/bed_arm_insert_flexi_rear.stl
models/BED ASSEMBLY/arms/bed_arm_left_flexi.stl
models/BED ASSEMBLY/arms/bed_arm_left_solid.stl
models/BED ASSEMBLY/arms/bed_arm_left_wobblex.stl
models/BED ASSEMBLY/arms/bed_arm_rear_flexi.stl
models/BED ASSEMBLY/arms/bed_arm_rear_flexi_triple.stl
models/BED ASSEMBLY/arms/bed_arm_rear_solid.stl
models/BED ASSEMBLY/arms/bed_arm_rear_solid_triple.stl
models/BED ASSEMBLY/arms/bed_arm_rear_wobblex.stl
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

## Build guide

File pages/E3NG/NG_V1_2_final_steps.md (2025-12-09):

---
title: Final steps
layout: default
has_children: true
nav_order: 50
parent: E3NG v1.2
permalink: /E3NG_v1_2/final_setup
---
# E3NG FINAL SETUP
{: .text-center }

{: .warning }
This page is under construction.

continue to:
{: .text-right .lh-0 .pt-8 }

[SETUP AND CALIBRATION]{: .btn .fs-6 .fw-300 .text-yellow-300 }
{: .text-right }

[SETUP AND CALIBRATION]: https://rh3d.xyz/setup.html

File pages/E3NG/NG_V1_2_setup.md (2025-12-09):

---
title: Setup and calibration
layout: default
parent: Final steps
#has_children: true
nav_order: 1
description: "Finalize your E3NG v1.2S build with setup and calibration tips. Dial in slicer settings, level your bed, and prepare for flawless CoreXY 3D printing."
permalink: /E3NG_v1_2/final_setup/setup_calibration
---
# PRINTER SETUP AND CALIBRATION
{: .text-center }

{: .warning }
This page is under construction and will be completed later.

# SLICER SETUP
{: .text-center }

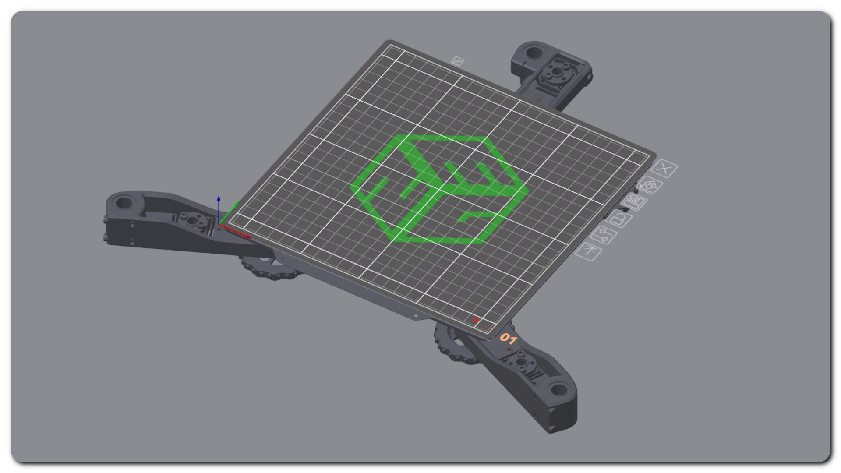
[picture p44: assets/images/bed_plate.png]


[BED PLATE TEXTURE .svg]{: .btn .fs-6 .fw-300 .text-yellow-300 .ml-7 .mr-4 .px-6 }
[BED MODEL .stl]{: .btn .fs-6 .fw-300 .text-yellow-300 .mr-7 .ml-4 .px-6 }
{: .text-center }

[BED PLATE TEXTURE .svg]: ../../assets/docs/E3NG_build_plate.svg
[BED MODEL .stl]: ../../assets/docs/E3NG_bed.stl

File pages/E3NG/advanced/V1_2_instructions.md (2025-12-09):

---
title: Build guide
layout: default
parent: v1.2 - (advanced)
grand_parent: E3NG v1.2
has_children: false
nav_order: 50
description: "Follow the build guide for advanced E3NG v1.2 CoreXY printers. Assemble modular parts with detailed instructions, tips, and supported configuration options."
permalink: /E3NG_v1_2/advanced/build_guide
---
# BUILD GUIDE
{: .text-center }

Below you can download the build manual for the E3NG v1.2.
It will guide you through the build process of the entire printer with many optional parts and build variations to cover most of the configuration options, but the enclosure process isn't covered in the current version.

Please read the instructions carefully, there may seem to be too many information but it covers many tips and helpful notes.

[E3NG v1.2 BUILD GUIDE]{: .btn .fs-6 .fw-300 .mt-8 .text-yellow-300 }
{: .text-center }
_last updated: 2025.01.16 12:40 (UTC +02:00)_{: .fs-3 .mt-0 .fw-300 }
{: .text-center }

### VIDEO BUILD GUIDES

<details>
    <summary><h4 style="display:inline-block;margin-left:1.5em"> Armor3D Printing </h4></summary>
    <p><a href="https://www.youtube.com/watch?v=CCZEbCcw1AA">Part 1 - Intro / Build guide overview</a></p>
    <p><a href="https://www.youtube.com/watch?v=qgxq2peSxVo">Part 2 - Bottom frame and bed carriage</a></p>
    <p><a href="https://www.youtube.com/watch?v=i3ZnNVzYnPM">Part 3 - Bed and AC heater</a></p>
    <p><a href="https://www.youtube.com/watch?v=FcIcflWklvw">Part 4 - Top frame</a></p>
    <p><a href="https://www.youtube.com/watch?v=30m1gHH1aQM">Part 5 - Frame and toolhead</a></p>
</details>

---

<details>
    <summary><h4 style="display:inline-block;margin-left:1.5em"> CHANGELOG </h4></summary>
    <p>2025.02.17 - Fixed pg.34 (Ender 3: screws) and pg.37 + pg.77 (M5x20 BHCS)</p>
    <p>2025.01.16 - Fixed pg.73 (2040 x 400 mm extrusion) and pg.74 DA=DB (~575 mm)</p>
    <p>2024.10.30 - Initial public release</p>
</details>

continue to:
{: .text-right .lh-0 .pt-8 }

[FIRMWARE]{: .btn .fs-6 .fw-300 .text-yellow-300 }
{: .text-right }

[E3NG v1.2 BUILD GUIDE]: ../../../assets/docs/Build_guide_E3NG_v1.2.pdf
[FIRMWARE]: https://rh3d.xyz/E3NG_v1_2/advanced/firmware

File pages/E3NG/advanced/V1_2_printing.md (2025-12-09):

---
title: Printing parts
layout: default
parent: v1.2 - (advanced)
grand_parent: E3NG v1.2
has_children: false
nav_order: 30
description: "Print parts for your advanced E3NG v1.2 CoreXY build with expert slicing settings, material tips, calibration guides, and color customization advice."
permalink: /E3NG_v1_2/advanced/printing_parts
---
# PRINTING PARTS
{: .text-center }

Before we dive into downloading all the files and starting the prints, it's important to be as prepared as possible. Nobody enjoys reprinting parts after the printer is already assembled and running. You'll need to choose the right material, ensure your printer is properly calibrated, and have the correct setup for printing. This all takes some time and effort, but it will save you plenty during the build and when using the printer, so try not to cut corners here.

And one of the least important things - you, of course, need to choose your colour combination.

---
# MATERIAL SELECTION

#### ABS/ASA
The most recommended and best choice material for printing parts. It has great properties to withstand increased temperatures, repeated stress and continuous pressure.
<details>
    <summary><h4 style="display:inline-block;margin-left:1.5em;margin-top:0.4em;color:#0096FF"> ABS PRINTING TIPS </h4></summary>
<ol style="margin-left:2em;font-size:14px">
<li>Use enclosure! - the best and the most effective step, even if you use some temporary solution to help eliminating drafts and increasing the ambient air temperature.</li>
<li>Use draft shield - without enclosure, draft shield will help to separate the cold air from the part itself. Draft shield may help even in enclosure when the air temperature is not high enough.</li>
<li>Clean the build plate - no alcohol wiping, use warm water with a dish soap and rub the build plate thoroughly. Wash it well too. Using rough side of the sponge helps.</li>
<li>Clamp your build plate - for magnetic flexible build plates. Your magnet may not be as strong as it used to be and bigger parts can lift the plate corners. Clamp the edges/corners of the build plate to the bed.</li>
<li>Use brim or mouse ears for better adhesion to the build plate.</li>
<li>Less is more - play with the print settings, you may need to decrease the fan speed and print speed.</li>
<li>More is more - try increasing the hotend temperature to properly melt the filament. Try increasing the bed temperature for better sticking parts and hotter environment for the print.</li>
<li>Use ABS+, ASA or a different brand - some filaments are more prone to warping, ASA overall tends to warp less. Do your research or testing to find better filament for you that could warp less.</li>
<li>Use adhesive - if your parts still don't stick to the surface, use some kind of bed adhesive suitable for ABS.</li>
<li>Avoid printing big parts, build the upgraded frame version with 2040 aluminium extrusions, build the "stock E3" or metal bed carriage.</li>
</ol>
</details>

#### PETG
Is significantly more flexible which will reduce stiffness of the frame. It has lower temperature resistance so enclosing the printer will get risky as some of the parts will most likely warp. If you do so, try using bed insulation and print at least the toolhead parts from ABS. It helps if you only print lower temperature materials like PLA and PETG.

#### PLA
Can be used on an open frame printer but not with an enclosure as the parts will definitely warp. The toolhead and bed
carriage should still be printer with higher temperature resistant material.

---
# PRINTING PARAMETERS

All STL files are properly oriented for printing. Some parts include built-in supports, they are marked with ❌.

Depending on your configuration and print settings (brim, draft, purge line), you may need to print bigger parts that require up to 235x235 mm print area. Default print size for Ender 3 is 220x220 mm but you can set it to 235x235 mm in slicer without issues.

#### RECOMMENDED PRINT SETTINGS:
<ul>
<li>4 perimeters</li>
<li>5 top and bottom layers</li>
<li>30% infill</li>
<li>infill type: cubic, gyroid, grid, honeycomb, 3D honeycomb, triangles, stars</li>
<li>0.2 mm layer height</li>
<li>0.4 - 0.5 mm layer width</li>
<li>Arachne slicing mode</li>
<li>No supports</li>
</ul>

---
# CALIBRATION PRINT AND TOLERANCES

Before printing parts, it is highly recommended to print the calibration cube. It contains essential features that are related to the project parts like holes for 8mm rods, for LM8LUU bearing, M3 and M5 heat inserts and some other print features to view the print quality.

All the parts are designed with rather tight tolerances (.2mm), so depending on your print quality and precision, it might cause too tight fit mainly on linear rods/bearings. If this is your case, you should clear the holes idealy with a reamer. You can also use properly sized drill bit or even a piece of fine-grit sandpaper on a round stick. Just proceed slowly and carefully so you don’t enlarge the holes too much, the ideal situation is to hand press the parts in with no noticeable play.

[DOWNLOAD THE CALIBRATION CUBE.]{: .btn .fw-400 .text-yellow-300 .v-align-middle .pr-4 .pl-4 }

---
# PRINTING PARTS IN COLOR

If you need help with choosing the colors for your printer, have a look at the [COLOR SCHEME] tool!

To follow the main/recommended color scheme, see the file names where each is marked either with **[A]** (accent) or **[M]** (main) as a color marker. But this is your printer, be creative and make your own color combination and design.

If you are installing LED lights, there are also diffusers that need to be printed with clean/transparent filament. These are marked with **[C]** (clear).

continue to:
{: .text-right .lh-0 .pt-8 }

[FILES]{: .btn .fs-6 .fw-300 .text-yellow-300 }
{: .text-right }

[COLOR SCHEME]: https://rh3d.xyz/E3NG_v1_2/color_scheme
[DOWNLOAD THE CALIBRATION CUBE.]: https://www.printables.com/en/model/478403
[FILES]: https://rh3d.xyz/E3NG_v1_2/advanced/files

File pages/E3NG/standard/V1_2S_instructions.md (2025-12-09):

---
title: Build guide
layout: default
parent: v1.2S - (standard)
grand_parent: E3NG v1.2
has_children: false
nav_order: 40
description: "Build your E3NG v1.2S CoreXY printer step by step. Download the official guide with detailed instructions, tips, and notes for a smooth DIY assembly."
permalink: /E3NG_v1_2/standard/build_guide
---
# BUILD GUIDE
{: .text-center }

Below you can download the build manual for the E3NG v1.2S.
It will guide you through the build process of the entire printer, but the enclosure process isn't covered in the current version.

Please read the instructions carefully, there may be a lot of information but it covers many tips and helpful notes.

[E3NG v1.2S BUILD GUIDE]{: .btn .fs-6 .fw-300 .mt-8 .text-yellow-300 }
{: .text-center }
_last updated: 2025.06.03 07:20 (UTC +02:00)_{: .fs-3 .mt-0 .fw-300 }
{: .text-center }

---

<details>
    <summary><h4 style="display:inline-block;margin-left:1.5em"> CHANGELOG </h4></summary>
    <p>2025.06.03 - Initial public release</p>
</details>

continue to:
{: .text-right .lh-0 .pt-8 }

[FIRMWARE]{: .btn .fs-6 .fw-300 .text-yellow-300 }
{: .text-right }

[FIRMWARE]: https://rh3d.xyz/E3NG_v1_2/standard/firmware
[E3NG v1.2S BUILD GUIDE]: ../../../assets/docs/Build_guide_E3NG_v1.2S.pdf

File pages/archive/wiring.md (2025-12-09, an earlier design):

---
title: General wiring
layout: default
parent: Printer electronics
#nav_order: 1
permalink: /wiring.html
---
# GENERAL WIRING
{: .text-center }

{: .warning }
This page is under construction.

continue to:
{: .text-right .lh-0 .pt-8 }

[KLIPPER FW]{: .btn .fs-6 .fw-300 .text-yellow-300 }
{: .text-right }

[MARLIN FW]{: .btn .fs-6 .fw-300 .text-yellow-300 }
{: .text-right }

[KLIPPER FW]: https://rh3d.xyz/klipper.html
[MARLIN FW]: https://rh3d.xyz/marlin.html

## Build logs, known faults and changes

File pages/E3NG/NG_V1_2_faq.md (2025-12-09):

---
title: FAQ
layout: default
parent: E3NG v1.2
#has_children: false
nav_order: 60
description: "Find answers to common questions about the E3NG v1.2 CoreXY conversion. Learn about STL files, BOM, manuals, CAD access, costs, and how to start your build."
permalink: /E3NG_v1_2/faq
---
# FREQUENTLY ASKED QUESTIONS
{: .text-center }

### GENERAL

<details>
    <summary><h4 style="display:inline-block;margin-left:1.5em"> WHERE DO I START? WHERE DO I FIND ALL THE IMPORTANT INFORMATIONS, FILES AND DOCUMENTS? </h4></summary>
<p>The main crossroad for the project is this website, where you will find all the important information and links to build the printer. I would recommend reading through the entire website starting with <a href="https://rh3d.xyz/">E3NG</a> and <a href="https://rh3d.xyz/into.html">Into the project</a>. If you want to get even deeper and be part of the community, <a href="https://discord.com/invite/Zkvu6uu2AR">join the Discord</a>.</p>
<p>Main STL files ready to print are hosted on <a href="https://www.printables.com/en/model/922401">Printables</a>.</p>
<p>CAD files are currently available through a small donation on <a href="https://ko-fi.com/rh3dcz">Ko-Fi</a>.</p>
</details>

<details>
    <summary><h4 style="display:inline-block;margin-left:1.5em"> WHERE IS THE BOM / BILL OF MATERIAL? </h4></summary>
<p>This project is using the <a href="https://rh3d.xyz/E3NG_v1_2/advanced/config">CONFIGURATOR</a>, which includes the BOM and other necessary things.</p>
</details>

<details>
    <summary><h4 style="display:inline-block;margin-left:1.5em"> IS THERE A BUILD MANUAL/INSTRUCTIONS? </h4></summary>
<p>There is a build manual for the beta version, link is on the <a href="https://www.printables.com/en/model/922401">Printables</a> page.</p>
<p>Build manual for the E3 NG v1.2 is currently not existent but will be made.</p>
</details>

<details>
    <summary><h4 style="display:inline-block;margin-left:1.5em"> IS THE PROJECT FREE? </h4></summary>
<p>The project is free for personal use and for use in a commercial environment (print farms, content making, presentational purposes) but it is not allowed to sell the project parts, files or assembly kits without a permission.</p>
<p>It is released under <a href="https://creativecommons.org/licenses/by-nc-sa/4.0/">CC BY-NC-SA 4.0 license</a>.</p>
<p>If you wish to sell kits or parts for the project, feel free to contact me through the <a href="https://rh3d.xyz/feedback.html">feedback</a>.</p>
</details>

<details>
    <summary><h4 style="display:inline-block;margin-left:1.5em"> WHAT DOES THE FREE PART OF THE PROJECT INCLUDE? </h4></summary>
<p>STL files for printing all the parts, CONFIGURATOR with BILL OF MATERIAL and PRINTED PARTS.</p>
<p>In the future, the BUILD MANUAL will also be included.</p>
</details>

<details>
    <summary><h4 style="display:inline-block;margin-left:1.5em"> CAN I GET THE CAD FILES? </h4></summary>
<p>Currently, CAD files are only available through a small donation on <a href="https://ko-fi.com/rh3dcz">Ko-Fi</a>.</p>
</details>

<details>
    <summary><h4 style="display:inline-block;margin-left:1.5em"> HOW MUCH DOES THE CONVERSION COST? </h4></summary>
<p>This is highly dependent on the choices you make while configuring your printer. For the best idea, it is recommend to open the <a href="https://rh3d.xyz/E3NG_v1_2/advanced/config">CONFIGURATOR</a> and set your preferred setup, it will automatically calculate the estimated price.</p>
<p> For the cheapest setup, the conversion price with BOM recommended parts can be around $ 240 (not incl. the filament price and the base printer).</p>
</details>

<details>
    <summary><h4 style="display:inline-block;margin-left:1.5em"> HOW MUCH FILAMENT DO I NEED? </h4></summary>
<p>How much filament you need is highly dependent on your choices but the <a href="https://rh3d.xyz/E3NG_v1_2/advanced/config">CONFIGURATOR</a> will automatically calculate the necessary amount.</p>
<p>PS You can change the M (main) or A (accent) color in the BOM to modify your color setup and see the changes.</p>
<p>PPS It is always good to expect failed prints and have extra filament.</p>
</details>

<details>
    <summary><h4 style="display:inline-block;margin-left:1.5em"> WHAT TYPE OF FILAMENT SHOULD I USE? </h4></summary>
<p>For filament recommendations and print instructions, look at <a href="https://rh3d.xyz/E3NG_v1_2/standard/printing_parts">PRINTING PARTS</a>.</p>
</details>

<details>
    <summary><h4 style="display:inline-block;margin-left:1.5em"> WHY DOES THE PROJECT USE LINEAR RODS AND NOT LINEAR RAILS? </h4></summary>
<p>Linear rods were chosen as a cheaper and more accessible option. They are also very reliable, tested and proven to work very well.</p>
<p>Me and some community members (mainly Mr. Puffington - thanks!) have been testing the performance of linear rods and compared to linear rail setup (user mod based on Voron Trident gantry), version with linear rods has been superior allowing higher accelerations with clean input shaper results.</p>
<p>There might be some changes or more options in the future though.</p>
</details>

<details>
    <summary><h4 style="display:inline-block;margin-left:1.5em"> WHAT FIRMWARE DOES THE PROJECT SUPPORT? </h4></summary>
<p>The project supports both Marlin and Klipper for selected boards, although the board compatibility will be getting wider.</p>
<p>Thanks to the use of DIN rails and the option to install universal cooling for the electronics, it is easy to install almost every board you can think of.</p>
</details>

<details>
    <summary><h4 style="display:inline-block;margin-left:1.5em"> SHOULD I CHOOSE MARLIN OR KLIPPER? </h4></summary>
<p>I think both firmwares are very similar in the daily use capabilities, both support the latest and high end features. Marlin benefits from running on a single board with a display controller that makes it a simple and solid setup with no added costs while Klipper supports more detailed tuning and with the added SBC it has more power to print faster. It is also simpler to reconfigure your printer without need to reflash the firmware, although Marlin has a lot of variables that can be changed without reflashing the FW.</p>
</details>

<details>
    <summary><h4 style="display:inline-block;margin-left:1.5em"> WILL I DESTROY MY ENDER 3? </h4></summary>
<p>No, this conversion will improve your Ender 3 in probably every way. If you decide to convert it just make sure and check at least twice that you have everything ready and that you understand what you are going to do. If you still decide that you liked your Ender 3 more than the Ender 3 NG, don't worry, the project is designed so that you don't make any changes to the original parts that would prevent you from rebuilding back to Ender 3.</p>
</details>

### PERFORMANCE

<details>
    <summary><h4 style="display:inline-block;margin-left:1.5em"> WHAT SPEEDS AND ACCELERATIONS CAN I EXPECT FROM THIS BUILD? </h4></summary>
<p>This is hugely dependent on the quality and precision of your build, used parts and the final tuning you will perform. Usually well build and well tuned printers are capable of printing at around 300-400 mm/s and 10-15K mm/s2 with pretty good quality. That is about as fast as you can get with the stock creality stepper motors.</p>
</details>

<details>
    <summary><h4 style="display:inline-block;margin-left:1.5em"> CAN I SEE THE INPUT SHAPER GRAPHS? </h4></summary>
<p>The IS result is a lot dependent on the build quality. Below I am posting some of my input shaper graphs.</p>
<p>    1. With printed frame verticals, no enclosure.</p>
<p>    2. With ultimate frame and enclosure (4mm panels + 5mm door).</p>
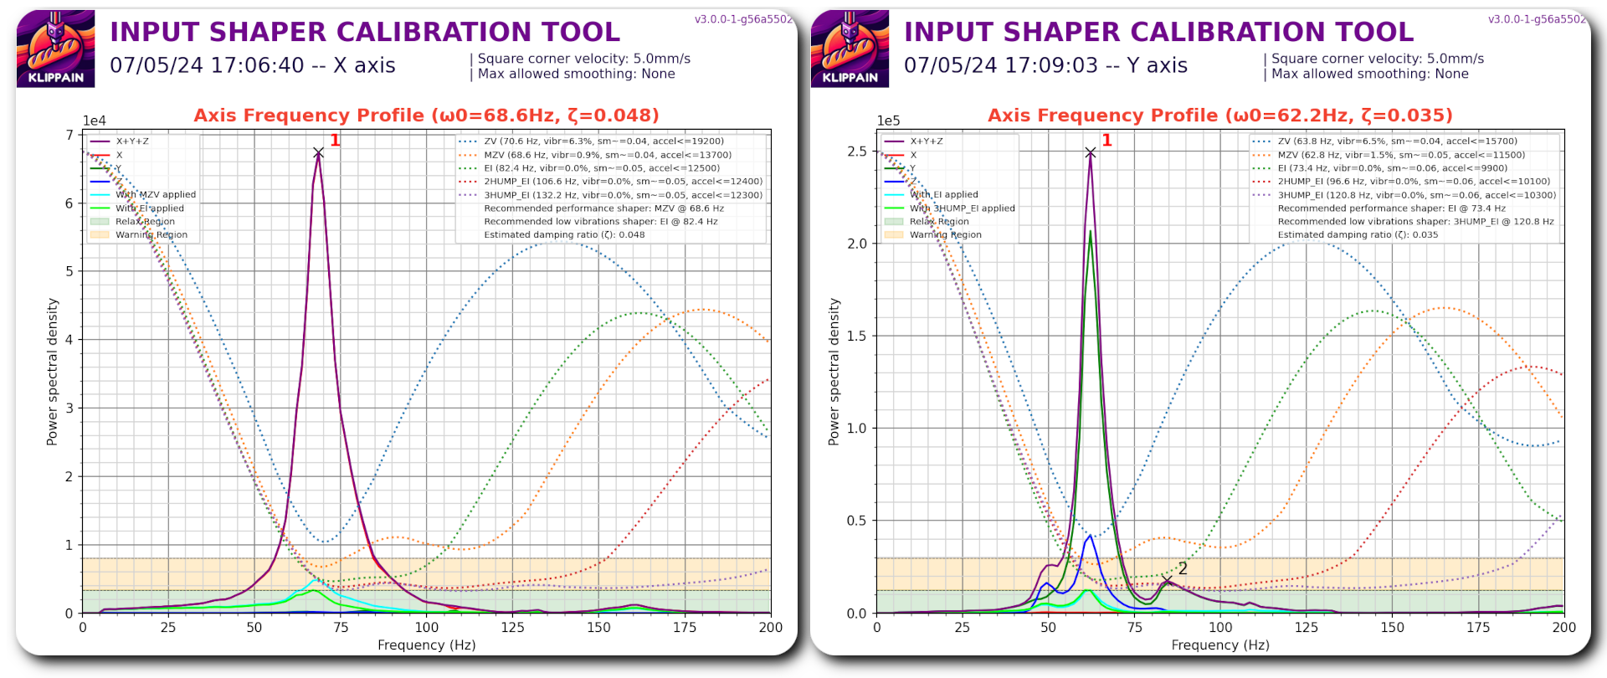
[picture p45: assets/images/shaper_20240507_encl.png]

</details>

### MECHANICAL

[Ender 3 NG]: https://rh3d.xyz/
[Into the project]: https://rh3d.xyz/into.html
[join the Discord]: https://discord.com/invite/Zkvu6uu2AR
[Printables]: https://www.printables.com/en/model/922401
[Ko-Fi]: https://ko-fi.com/rh3dcz
[CONFIGURATOR]: https://rh3d.xyz/E3NG_v1_2/advanced/config
[PRINTING PARTS]: https://rh3d.xyz/E3NG_v1_2/standard/printing_parts

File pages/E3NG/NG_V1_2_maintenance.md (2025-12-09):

---
#title: Printer maintenance
layout: default
parent: Final steps
#has_children: true
nav_order: 20
description: "Maintain your E3NG v1.2 CoreXY printer with expert tips on calibration, cleaning, firmware, and troubleshooting. Keep your DIY build precise and reliable."
permalink: /E3NG_v1_2/final_setup/maintenance
---
# PRINTER MAINTENANCE
{: .text-center }

{: .warning }
This page is under construction.
